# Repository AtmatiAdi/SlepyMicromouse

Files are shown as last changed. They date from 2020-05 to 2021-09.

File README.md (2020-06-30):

# OpisProjektu

Głównym celem projektu jest stworzenie Micromouse który będzie posiadał tylko akcelerometr i żyroskop do rozpoznawania położenia przeszkód i położenia samego robota. Takie rozwiązanie jest niekonwencjonalne gdyż z reguły wszystkie roboty tego typu posiadają czujniki optyczne do wykrywania przeszkód. Micromouse to kategoria robotów których zadaniem jest wydostanie się z labiryntu, ten robot będzie miał takie samo zadanie lecz strategia wyszukiwania wyjścia z labiryntu będzie inna niż standardowo. Robot aby zidentyfikować ściany które są dookoła niego musi w nie stuknąć, nie za mocno by nie uszkodzić labiryntu, a zamantowany akcelerometr wykryje kierunek uderzenia i tak będzie wiadomo gdzie znajduje się przeszkoda. Wykrycie kierunku uderzenia nie jest trywialne więc do tego posłuży specjalnie zamontowana obręcz na sprężynie która da niewielkie możliwości ruchowe, tak aby przy uderzeniu obrącz lekko się przesunęła i akcelerometr na niej zamontowany mógł poprawnie odczytać przesunięcie. Ruchoma obręcz jest potrzebna gdyż zakładamy że koła nie mają poślizgu, więc wykrycie kierunku byłoby utrudnione. żyroskop daje możliwość odczytu obrotu całego robota, wszystko to jest potrzebne ponieważ robot nie będzie miał enkoderów ani innych sensorów które pozwolą sledzić jego przemieszczenie.

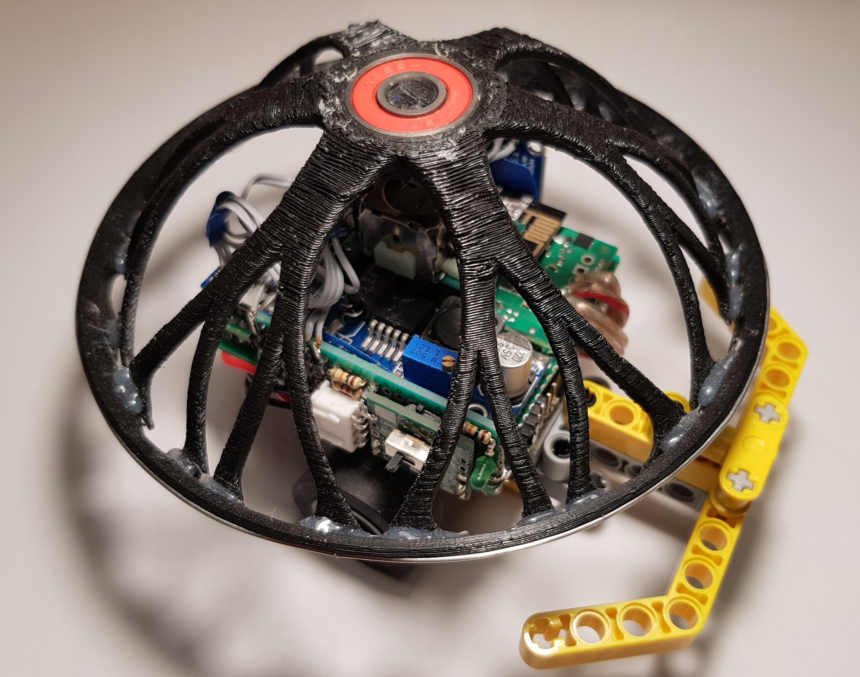
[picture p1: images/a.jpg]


Robot posiada mikrokontroler STM32F103 i sensor MPU-6050. Silniki dobrane będą tak by robot dostatecznie precyzyjnie mógł się poruszać, koła dobrane są tak aby zapewnić przyczepność i móc między innymi w algorytmie wykluczyć poślizg. Dodatkowo wykorzystany zostanie moduł nRF24L01 do komunikacji zdalnej, aby robotem sterować i pobierać od niego informacje sensoryczne, będzie to część na projekt wizualizacja danych sensorycznych. Dodatkowo pomiar napięcia baterii by zabezpieczyć baterie przed rozładowaniem. Moduł mikrokontrolera zawiera stabilizator, tak jak IMU czy moduł radiowy, więc na schemacie zostatał on pominięty.

Sensor MPU-6050 Jest 3 osiowym akcelerometrem i 3 osiowym żyroskopem w jednym, komunikacja z nim przebiega przez magistralę I2C
moduł nRF24L01 To moduł radiowy 2.4Ghz, komunikacja z nim odbywa się poprzez magistralę SPI
Schemat modułowy robota przedstawia rysunek:

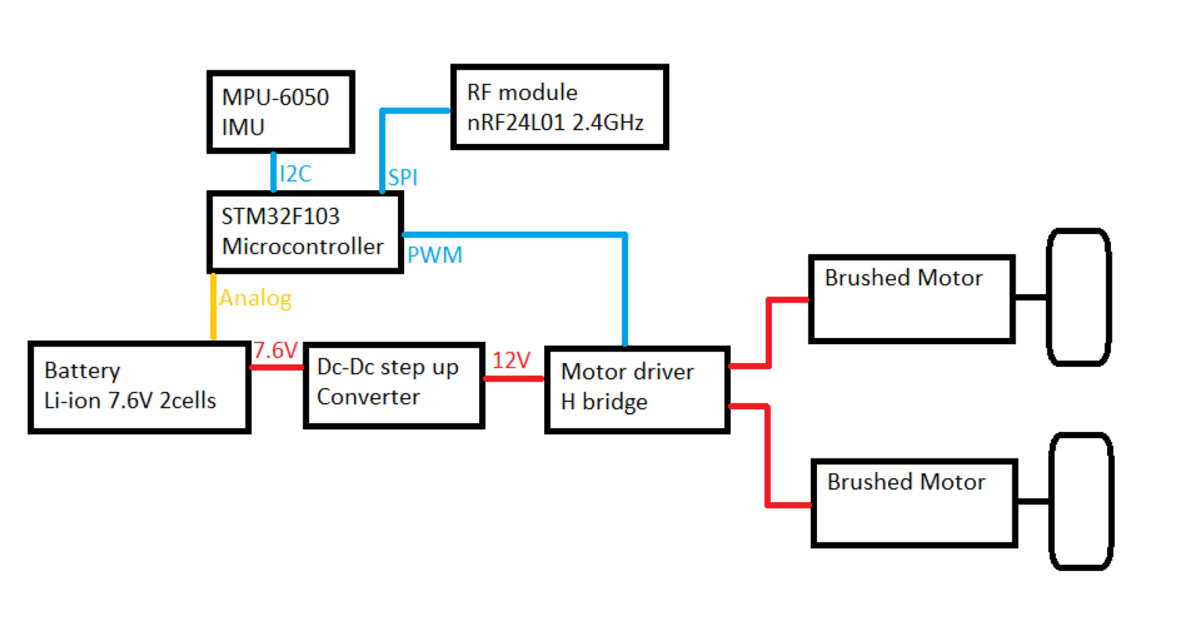
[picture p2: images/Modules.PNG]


# Algorytm Micromouse
Algorytm ma za zadanie wykrywać ściany w labiryncie i zapamiętywać ich ustawienie w pamięci, po odkryciu całego labiryntu wyznaczana będzie ścieżka optymalna z punktu startowego do centrum labiryntu, czyli mety. Następnie robot będzie musiał przebyć wyznaczoną ścieżkę jak najszybciej. Algorytm został zaimplementowany w aplikacji. Takie rozwiązanie bardzo usprawniło tworzenie algorytmu. Istotne jest to że wymiana danych mimo swej prędkości nie jest wstanie zapewnić dokładności w takich operacjach jak przemieszczanie się czy obracanie, liczenie podwójnej całki z tak otrzymywanych danych byłoby bezużyteczne, robot więc posiada funkcje do przemieszczania się i obrotu samodzielnie, zapewnia to dokładność. Jazda o zadane przemieszczenie odbywa się poprzez dostarczenie też informacje o wartości progowej przyspieszenia które oznaczałoby zderzenie się z przeszkodą, niezależnie od przyczyny zakończenia ruchu, robot wysyła wartość przemieszczenia jaką udało mu się wyliczyć na podstawie odczytów z akcelerometru. Podczas obrotu nie podaje się warunku stopu. Uzyskana dokładność obrotu jest bardzo zadowalająca, lecz przemieszczanie się jest obarczone takim błędem że nie możliwe jest zadanie robotowi przemieszczenia większego niż 18 cm (rozmiar jednej komórki labiryntu) bez błędu na tyle dużego który zakłóci działanie algorytmu. Problem ten rozwiązuje sposób przemieszczania się w którym robot zawsze przemieszcza się najdalej jak potrafi, algorytm dostając informację zwrotną dopasowywać ją do labiryntu, jednak takie rozwiązanie powoduje następny problem, robot będzie mógł wpaść w pułapki z których nie będzie dało się w ten sposób wyjechać, rozwiązaniem jest połączenie tych dwóch taktyk tak by algorytm sam decydował o sposobie przemieszczania się.

# Linki

https://youtu.be/gzY4Sm2h51A - Prezentacja ukończenia projektu

https://www.overleaf.com/read/rbngfpkfhwbz - Raport końcowy

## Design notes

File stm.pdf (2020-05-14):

## stm Project Configuration Report

# 1. Description

## 1.1. Project

Project Name | stm
Board Name | No information
Generated with: | STM32CubeMX 4.24.0
Date | 03/13/2020

## 1.2. MCU

MCU Series | STM32F1
MCU Line | STM32F103
MCU name | STM32F103CBTx
MCU Package | LQFP48
MCU Pin number | 48

# 2. Pinout Configuration

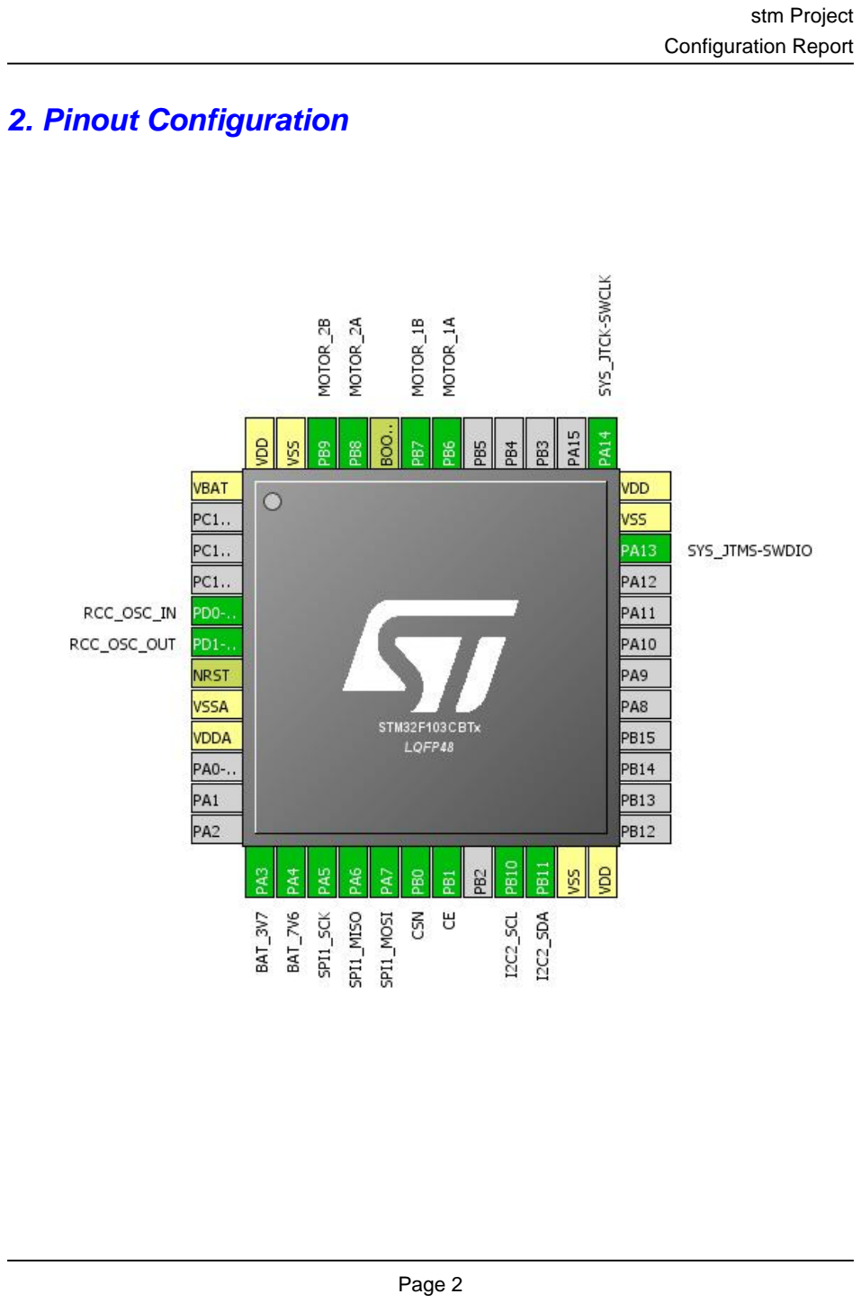
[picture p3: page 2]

# 3. Pins Configuration

Pin Number LQFP48 | Pin Name (function after reset) | Pin Type | Alternate Function(s) | Label
1 | VBAT | Power
5 | PD0-OSC_IN | I/O | RCC_OSC_IN
6 | PD1-OSC_OUT | I/O | RCC_OSC_OUT
7 | NRST | Reset
8 | VSSA | Power
9 | VDDA | Power
13 | PA3 | I/O | ADC1_IN3 | BAT_3V7
14 | PA4 | I/O | ADC1_IN4 | BAT_7V6
15 | PA5 | I/O | SPI1_SCK
16 | PA6 | I/O | SPI1_MISO
17 | PA7 | I/O | SPI1_MOSI
18 | PB0 * | I/O | GPIO_Output | CSN
19 | PB1 * | I/O | GPIO_Output | CE
21 | PB10 | I/O | I2C2_SCL
22 | PB11 | I/O | I2C2_SDA
23 | VSS | Power
24 | VDD | Power
34 | PA13 | I/O | SYS_JTMS-SWDIO
35 | VSS | Power
36 | VDD | Power
37 | PA14 | I/O | SYS_JTCK-SWCLK
42 | PB6 | I/O | TIM4_CH1 | MOTOR_1A
43 | PB7 | I/O | TIM4_CH2 | MOTOR_1B
44 | BOOT0 | Boot
45 | PB8 | I/O | TIM4_CH3 | MOTOR_2A
46 | PB9 | I/O | TIM4_CH4 | MOTOR_2B
47 | VSS | Power
48 | VDD | Power

## * The pin is affected with an I/O function

# 4. Clock Tree Configuration

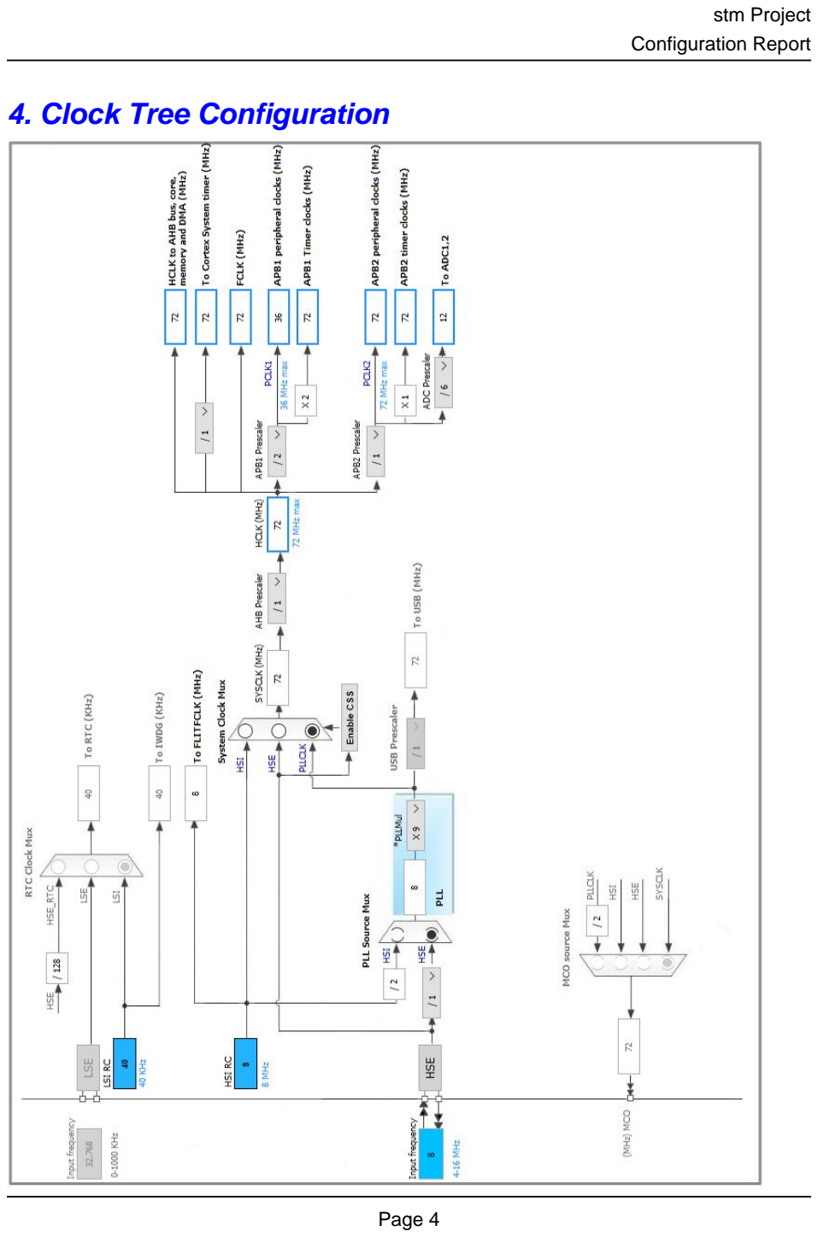
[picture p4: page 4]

# 5. IPs and Middleware Configuration

# 5.1. ADC1

## mode: IN3 mode: IN4

## 5.1.1. Parameter Settings:

### ADCs_Common_Settings:

Mode | Independent mode

### ADC_Settings:

Data Alignment | Right alignment
Scan Conversion Mode | Disabled
Continuous Conversion Mode | Disabled
Discontinuous Conversion Mode | Disabled

### ADC_Regular_ConversionMode:

Enable Regular Conversions | Enable
Number Of Conversion | 1
External Trigger Conversion Source | Regular Conversion launched by software
Rank | 1
Channel | Channel 3
Sampling Time | 1.5 Cycles

### ADC_Injected_ConversionMode:

Number Of Conversions | 0

### WatchDog:

Enable Analog WatchDog Mode | false

# 5.2. I2C2

## I2C: I2C

## 5.2.1. Parameter Settings:

### Master Features:

I2C Speed Mode | Standard Mode
I2C Clock Speed (Hz) | 100000

### Slave Features:

Clock No Stretch Mode | Disabled
Primary Address Length selection | 7-bit
Dual Address Acknowledged | Disabled
Primary slave address | 0
General Call address detection | Disabled

# 5.3. RCC

## High Speed Clock (HSE): Crystal/Ceramic Resonator

## 5.3.1. Parameter Settings:

### System Parameters:

VDD voltage (V) | 3.3
Prefetch Buffer | Enabled
Flash Latency(WS) | 2 WS (3 CPU cycle)

### RCC Parameters:

HSI Calibration Value | 16
HSE Startup Timout Value (ms) | 100
LSE Startup Timout Value (ms) | 5000

# 5.4. SPI1

## Mode: Full-Duplex Master

## 5.4.1. Parameter Settings:

### Basic Parameters:

Frame Format | Motorola
Data Size | 8 Bits
First Bit | MSB First

### Clock Parameters:

Prescaler (for Baud Rate) | 4 *
Baud Rate | 18.0 MBits/s *
Clock Polarity (CPOL) | Low
Clock Phase (CPHA) | 1 Edge

### Advanced Parameters:

CRC Calculation | Disabled

NSS Signal Type | Software

# 5.5. SYS

## Debug: Serial Wire Timebase Source: SysTick

# 5.6. TIM4

## Channel1: PWM Generation CH1 Channel2: PWM Generation CH2 Channel3: PWM Generation CH3 Channel4: PWM Generation CH4

## 5.6.1. Parameter Settings:

### Counter Settings:

Prescaler (PSC - 16 bits value) | 0
Counter Mode | Up
Counter Period (AutoReload Register - 16 bits value ) | 0
Internal Clock Division (CKD) | No Division
auto-reload preload | Disable

### Trigger Output (TRGO) Parameters:

Master/Slave Mode (MSM bit) | Disable (Trigger input effect not delayed)
Trigger Event Selection | Reset (UG bit from TIMx_EGR)

### PWM Generation Channel 1:

Mode | PWM mode 1
Pulse (16 bits value) | 0
Fast Mode | Disable
CH Polarity | High

### PWM Generation Channel 2:

Mode | PWM mode 1
Pulse (16 bits value) | 0
Fast Mode | Disable
CH Polarity | High

### PWM Generation Channel 3:

Mode | PWM mode 1
Pulse (16 bits value) | 0
Fast Mode | Disable
CH Polarity | High

### PWM Generation Channel 4:

Mode | PWM mode 1
Pulse (16 bits value) | 0
Fast Mode | Disable
CH Polarity | High

### * User modified value

# 6. System Configuration

# 6.1. GPIO configuration

IP | Pin | Signal | GPIO mode | GPIO pull/up pull down | Max Speed | User Label
ADC1 | PA3 | ADC1_IN3 | Analog mode | n/a | n/a | BAT_3V7
| PA4 | ADC1_IN4 | Analog mode | n/a | n/a | BAT_7V6
I2C2 | PB10 | I2C2_SCL | Alternate Function Open Drain | n/a | High *
| PB11 | I2C2_SDA | Alternate Function Open Drain | n/a | High *
RCC | PD0-OSC_IN | RCC_OSC_IN | n/a | n/a | n/a
| PD1-OSC_OUT | RCC_OSC_OUT | n/a | n/a | n/a
SPI1 | PA5 | SPI1_SCK | Alternate Function Push Pull | n/a | High *
| PA6 | SPI1_MISO | Input mode | No pull-up and no pull-down | n/a
| PA7 | SPI1_MOSI | Alternate Function Push Pull | n/a | High *
SYS | PA13 | SYS_JTMS-SWDIO | n/a | n/a | n/a
| PA14 | SYS_JTCK-SWCLK | n/a | n/a | n/a
TIM4 | PB6 | TIM4_CH1 | Alternate Function Push Pull | n/a | Low | MOTOR_1A
| PB7 | TIM4_CH2 | Alternate Function Push Pull | n/a | Low | MOTOR_1B
| PB8 | TIM4_CH3 | Alternate Function Push Pull | n/a | Low | MOTOR_2A
| PB9 | TIM4_CH4 | Alternate Function Push Pull | n/a | Low | MOTOR_2B
GPIO | PB0 | GPIO_Output | Output Push Pull | n/a | Low | CSN
| PB1 | GPIO_Output | Output Push Pull | n/a | Low | CE

# 6.2. DMA configuration

## nothing configured in DMA service

# 6.3. NVIC configuration

Interrupt Table | Enable | Preenmption Priority | SubPriority
Non maskable interrupt | true | 0 | 0
Hard fault interrupt | true | 0 | 0
Memory management fault | true | 0 | 0
Prefetch fault, memory access fault | true | 0 | 0
Undefined instruction or illegal state | true | 0 | 0
System service call via SWI instruction | true | 0 | 0
Debug monitor | true | 0 | 0
Pendable request for system service | true | 0 | 0
System tick timer | true | 0 | 0
PVD interrupt through EXTI line 16 | unused
Flash global interrupt | unused
RCC global interrupt | unused
ADC1 and ADC2 global interrupts | unused
TIM4 global interrupt | unused
I2C2 event interrupt | unused
I2C2 error interrupt | unused
SPI1 global interrupt | unused

### * User modified value

# 7. Power Consumption Calculator report

### 7.1. Microcontroller Selection

Series | STM32F1
Line | STM32F103
MCU | STM32F103CBTx
Datasheet | 13587_Rev17

### 7.2. Parameter Selection

Temperature | 25
Vdd | 3.3

# 8. Software Pack Report

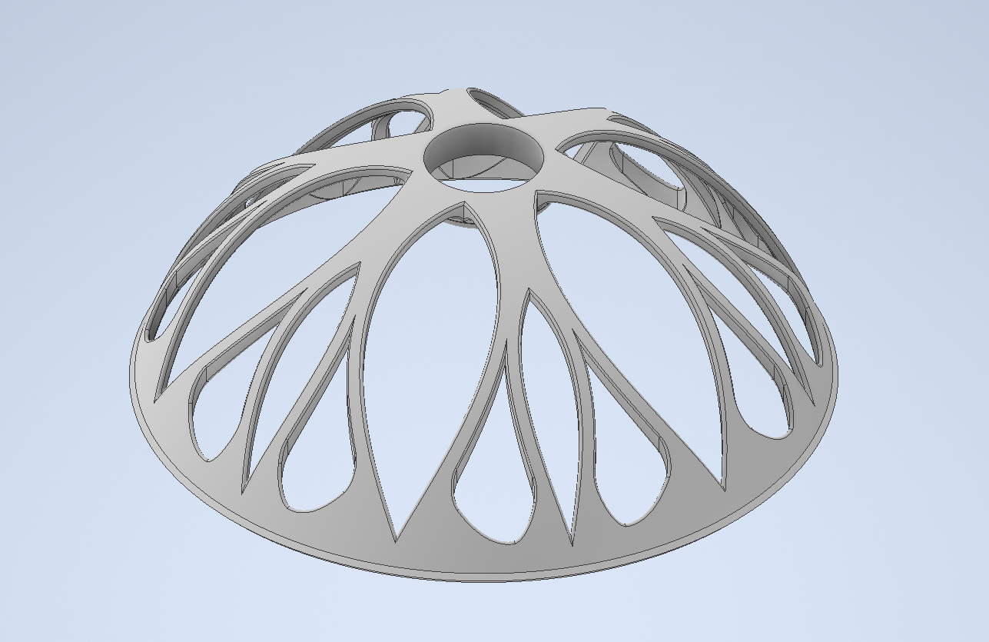
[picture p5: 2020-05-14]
images/obudowa_1.PNG

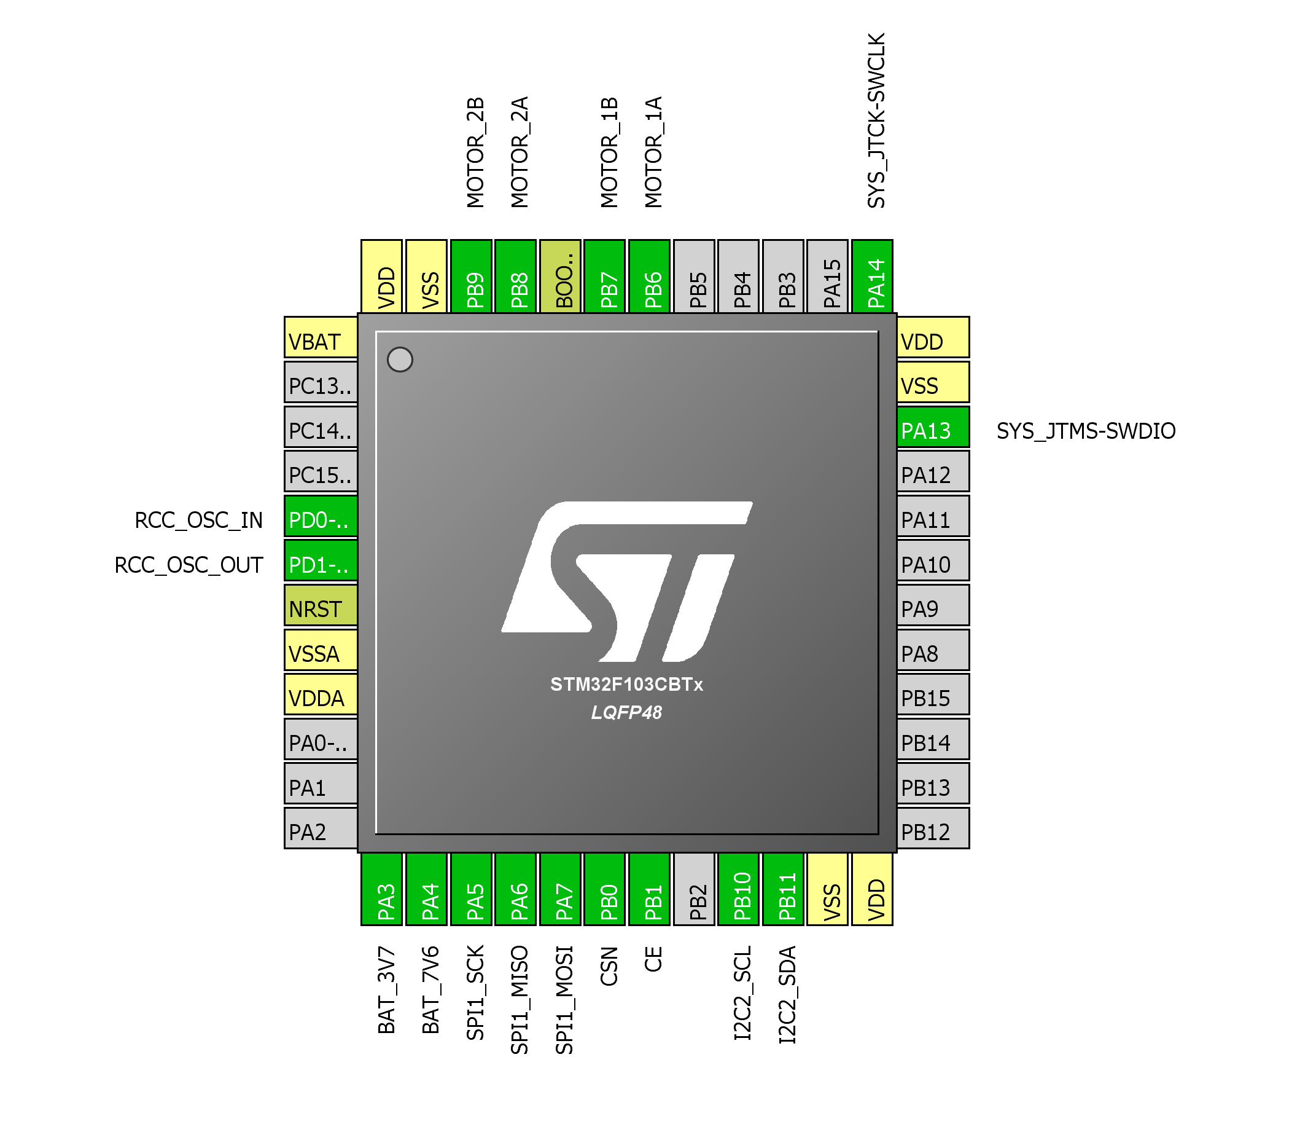
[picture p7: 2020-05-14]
images/cpu.PNG

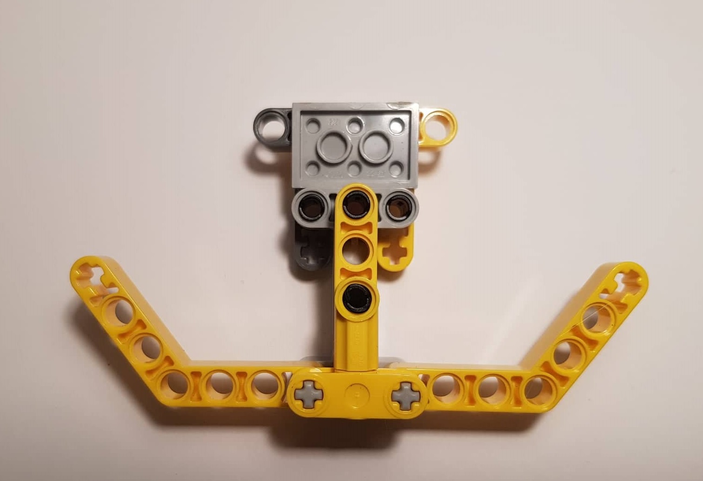
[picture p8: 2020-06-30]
images/lego.jpg

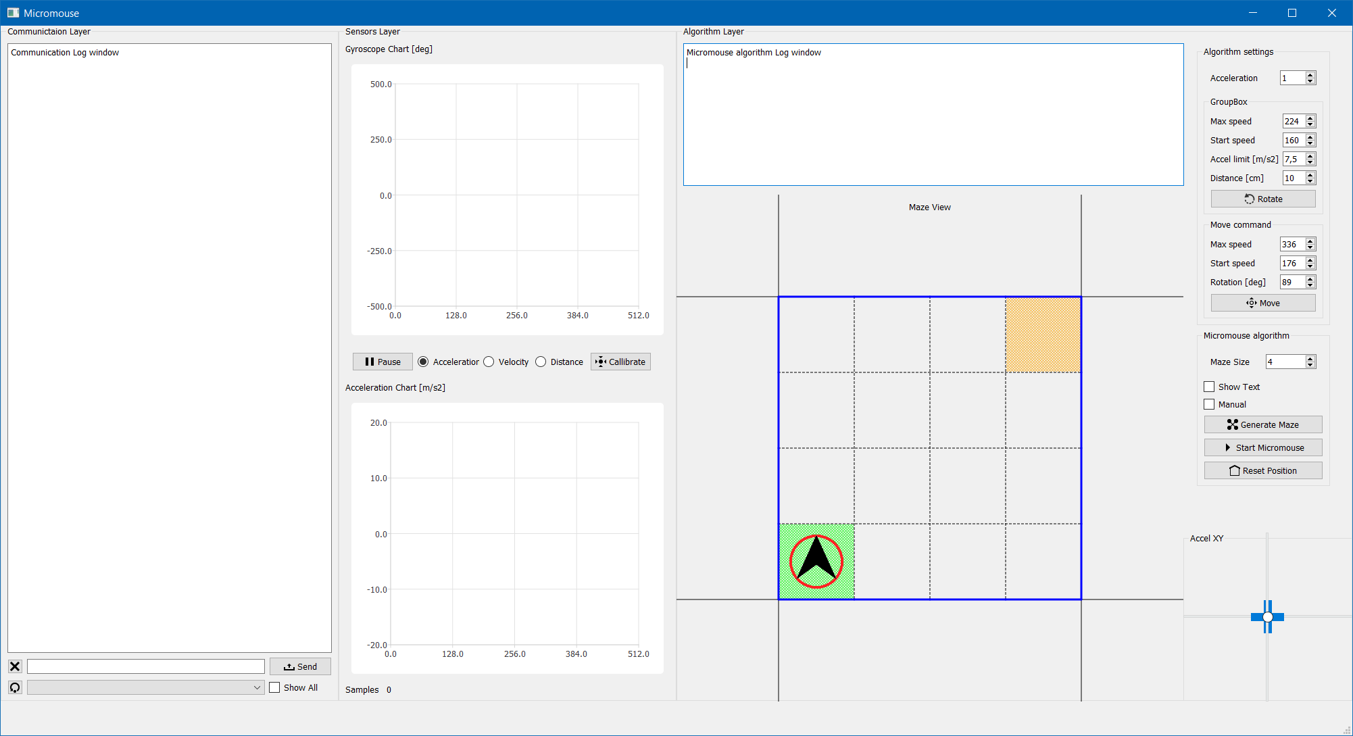
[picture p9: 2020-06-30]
images/apk.PNG

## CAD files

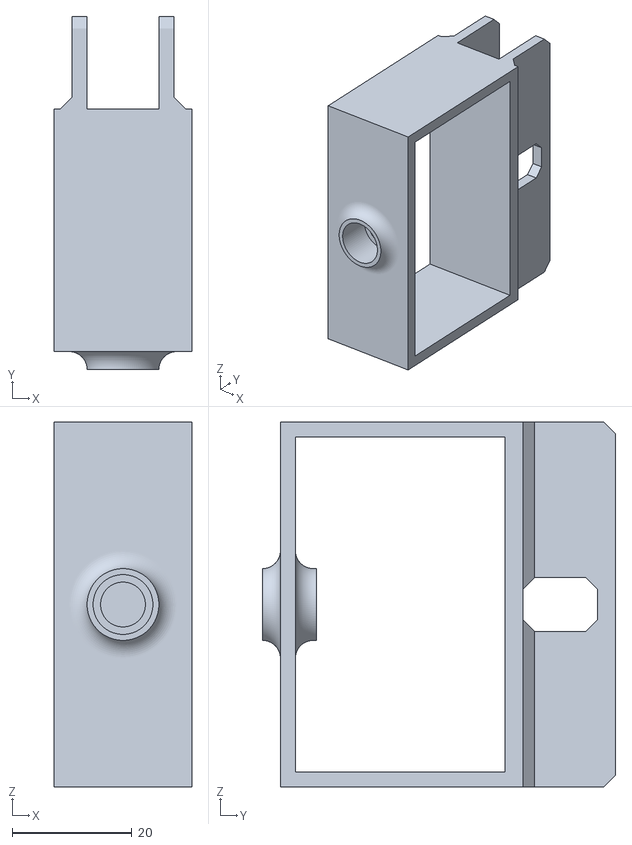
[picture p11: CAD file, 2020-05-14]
Czesci/Koszyk_v2.obj
23.0 x 59.0 x 61.0

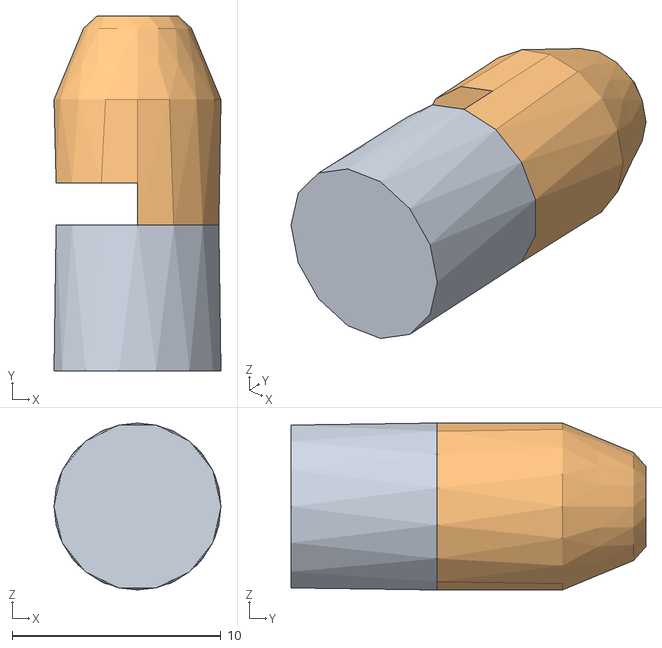
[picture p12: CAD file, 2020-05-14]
Czesci/Czopek.obj
8.00 x 17.0 x 8.00

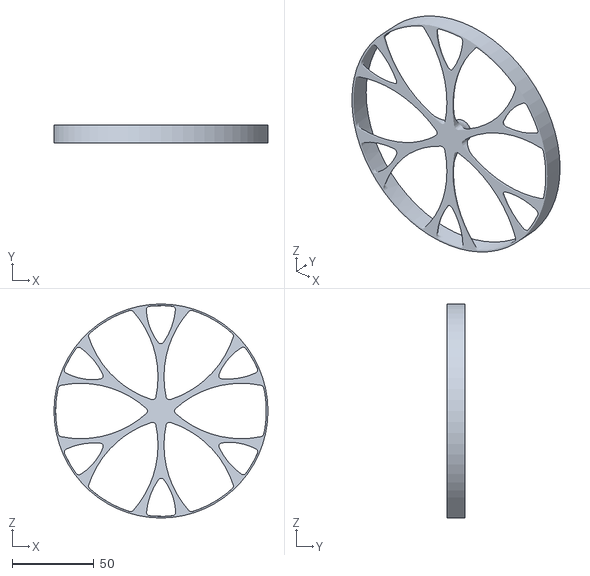
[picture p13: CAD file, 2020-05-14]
Czesci/czujka.obj
131.1 x 11.0 x 131.1

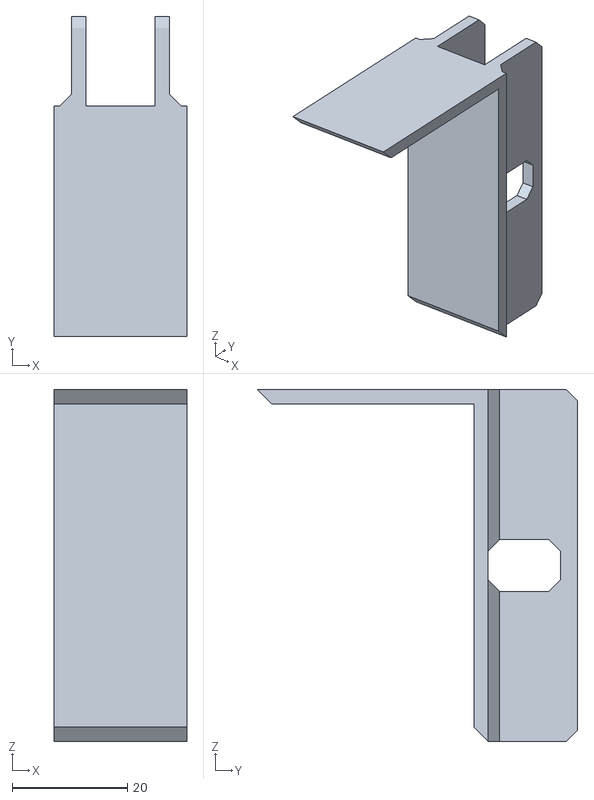
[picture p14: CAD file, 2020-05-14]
Czesci/Koszyk_v2_p1.obj
23.0 x 55.5 x 61.0

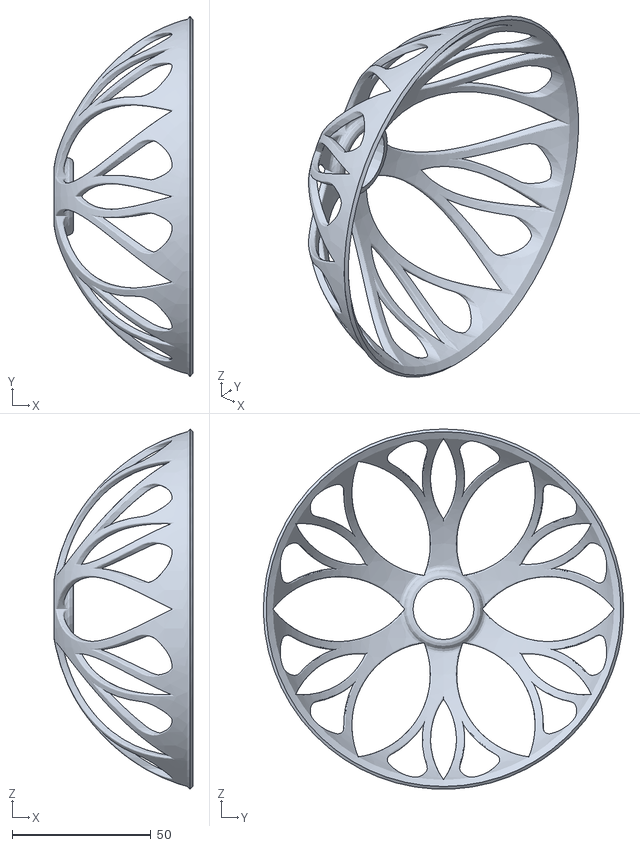
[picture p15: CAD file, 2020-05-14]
Czesci/czujka_v3.obj
50.0 x 130.0 x 129.9

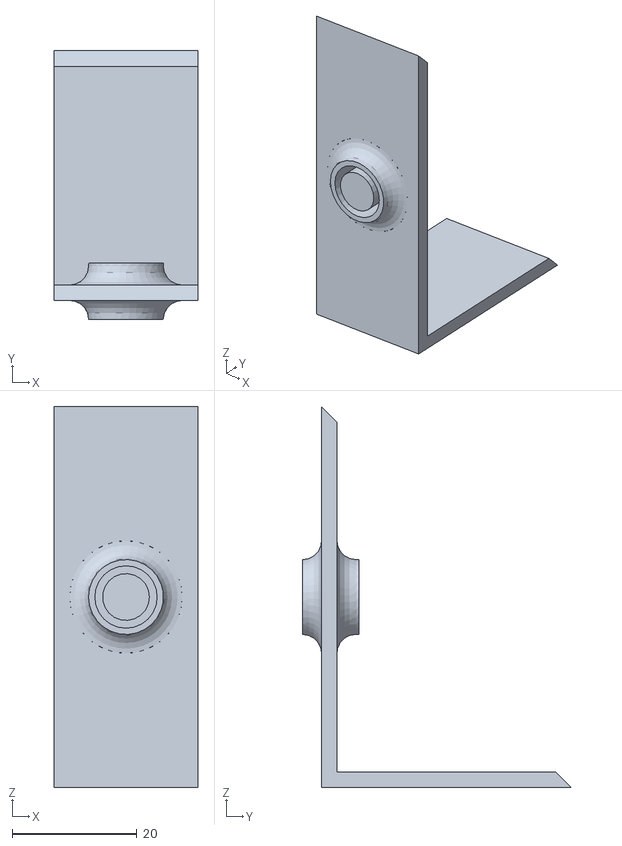
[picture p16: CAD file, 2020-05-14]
Czesci/Koszyk_v2_p2.obj
23.0 x 43.0 x 61.0

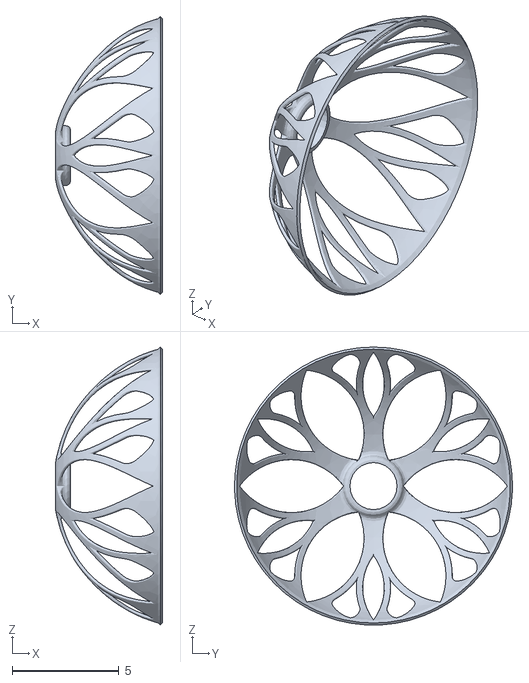
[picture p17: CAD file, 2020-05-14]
Czesci/czujka_v2.stl
5.00 x 13.0 x 13.0

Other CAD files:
Czesci/Koszyk_v2_part.dwg
Czesci/Czopek.ipt
Czesci/Koszyk.ipt
Czesci/Koszyk_v2.ipt
Czesci/Main.ipt
Czesci/OldVersions/Assembly.0011.iam
Czesci/OldVersions/Koszyk.0001.ipt
Czesci/OldVersions/Koszyk_v2.0004.ipt
Czesci/OldVersions/czujka.0005.ipt
Czesci/OldVersions/czujka_v2.0009.ipt
Czesci/OldVersions/mouse.0001.iam
Czesci/czujka.ipt
Czesci/czujka_v2.dwg
Czesci/czujka_v2.ipt
Czesci/czujka_v2.obj
Czesci/frame.ipt
Czesci/mouse.iam

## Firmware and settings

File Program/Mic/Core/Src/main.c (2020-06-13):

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

/* Includes ------------------------------------------------------------------*/
#include "main.h"

/* USER CODE BEGIN Includes */
#include "MY_NRF24.h"
#include "ssd1306.h"
#include "i2c-lcd.h"
#include "string.h"
#include "my_icons.h"
//#include "TJ_MPU6050.h"
#include "AccelGyro.h"

/* USER CODE END Includes */

/* USER CODE BEGIN PTD */
// Funkcja to paczka danych
#define FUNC_ACCEL_GYRO_DATA	128
#define FUNC_JOYSTICK_DATA		129
#define FUNC_ACCEL_GYRO_COMBO	130
// Tryb to trybie pracy
#define MODE_ACCELERATION_BURST 160
#define MODE_VELOCITY_BURST		161
#define MODE_DISTANCE_BURST		162
// Program to jakies zadanie do zrealizowania
#define PROG_CALLIBRATE			192
#define PROG_RESET_VEL_DIST		193
#define PROG_MOVE_BREAK			194
#define PROG_ROTATE				195
// Odpowiedz ze cos gotowe i zwraca wartosc
#define OK						255



/* USER CODE END PTD */

ADC_HandleTypeDef hadc1;

I2C_HandleTypeDef hi2c2;

SPI_HandleTypeDef hspi1;

TIM_HandleTypeDef htim2;
TIM_HandleTypeDef htim3;
TIM_HandleTypeDef htim4;

UART_HandleTypeDef huart1;

void SystemClock_Config(void);
static void MX_GPIO_Init(void);
static void MX_ADC1_Init(void);
static void MX_I2C2_Init(void);
static void MX_SPI1_Init(void);
static void MX_TIM4_Init(void);
static void MX_USART1_UART_Init(void);
static void MX_TIM2_Init(void);
static void MX_TIM3_Init(void);
/* USER CODE BEGIN 0 */
uint64_t PipeAddres = 0x11223344AA;
char Msg[32] = "HI";
char RF_RxData[32];
int Flag = 0;
int Counter = 0;
int mode = MODE_ACCELERATION_BURST;


void MotorSetValue(int16_t Left, int16_t Right)
{
	if (Right > 0) {
		SetPwm(Right, 3);
		SetPwm(0, 4);
	} else {
		SetPwm(0, 3);
		SetPwm(-1 * Right, 4);
	}
	if (Left > 0) {
		SetPwm(Left, 2);
		SetPwm(0, 1);
	} else {
		SetPwm(0, 2);
		SetPwm(-1 * Left, 1);
	}
}

void SetPwm(uint16_t Value, uint16_t Channel) {
    TIM_OC_InitTypeDef sConfigOC;

    sConfigOC.OCMode = TIM_OCMODE_PWM1;
    sConfigOC.Pulse = Value;
    sConfigOC.OCPolarity = TIM_OCPOLARITY_HIGH;
    sConfigOC.OCFastMode = TIM_OCFAST_DISABLE;

    switch(Channel) {
    case 1: {
    	HAL_TIM_PWM_ConfigChannel(&htim4, &sConfigOC, TIM_CHANNEL_1);
		HAL_TIM_PWM_Start(&htim4, TIM_CHANNEL_1);
		break;
    }
    case 2: {
		HAL_TIM_PWM_ConfigChannel(&htim4, &sConfigOC, TIM_CHANNEL_2);
		HAL_TIM_PWM_Start(&htim4, TIM_CHANNEL_2);
		break;
	}
    case 3: {
		HAL_TIM_PWM_ConfigChannel(&htim4, &sConfigOC, TIM_CHANNEL_3);
		HAL_TIM_PWM_Start(&htim4, TIM_CHANNEL_3);
		break;
	}
    case 4: {
		HAL_TIM_PWM_ConfigChannel(&htim4, &sConfigOC, TIM_CHANNEL_4);
		HAL_TIM_PWM_Start(&htim4, TIM_CHANNEL_4);
		break;
	}
    default : {
    	// Blad XDD
    	break;
    }
    }

}

double MapValue(double Val, double FromLow,double FromHigh,double ToLow,double ToHigh){
	return ToLow + ((ToHigh - ToLow) / (FromHigh - FromLow)) * (Val - FromLow);
}

double MapValue2(double input, double input_start,double input_end,double output_start,double output_end) {
	double slope = 1.0 * (output_end - output_start) / (input_end - input_start);
	return output_start + slope * (input - input_start);
}

void HAL_TIM_PeriodElapsedCallback(TIM_HandleTypeDef *htim){
	if (htim->Instance == htim3.Instance){
		Flag = 1;
	}
}

int Serial_Send(uint8_t* Buf, uint32_t *Len){
	CDC_Transmit_FS(Buf, Len);
	return &Len;
}

void SendInt(int Number){
	char in[10], out[10];
	int a = 0;
	int num;
	while ((Number / 10 > 0) || (Number % 10) > 0){
		num = (Number % 10);
		in[a] = num + '0';
		Number = Number / 10;
		a++;
	}
	//for (int b = a - 1; b >= 0; b--) {
	//	out[a - 1 - b] = in[b];
	//}
	if (a > 0) {
		CDC_Transmit_FS(in, a);
	}
}

void SendReturn(short val){
	Msg[0] = OK;
	Msg[1] = val;
	Msg[2] = val >> 8;
	if (NRF24_write(Msg, 3))
	  {
		  //HAL_Delay(1);
		  NRF24_read(RF_RxData, 16);
	  }
}

void AdcRead(int16_t *buf){
	HAL_ADC_Start(&hadc1);
	if (HAL_ADC_PollForConversion(&hadc1, 1000) == HAL_OK) {
		buf[0] = HAL_ADC_GetValue(&hadc1);
	}
	if (HAL_ADC_PollForConversion(&hadc1, 1000) == HAL_OK) {
		buf[1] = HAL_ADC_GetValue(&hadc1);
	}
	if (HAL_ADC_PollForConversion(&hadc1, 1000) == HAL_OK) {
		buf[1] = HAL_ADC_GetValue(&hadc1);
	}
	HAL_ADC_Stop(&hadc1);
}

void UlToStr(char *s, unsigned long bin, unsigned char n)
{
    s += n;
    *s = '\0';

    while (n--)
    {
        *--s = (bin % 10) + '0';
        bin /= 10;
    }
}

void Update_SSD(){
	// Ikona naładowania
	int16_t Val[3];
	AdcRead(Val);
	Val[0] = MapValue(Val[0], 0,4095 , 0, 1000);
	Val[1] = MapValue(Val[1], 0,4095 , 0, 1000);
	//Val[0] -= Val[1];
	char val[5];

	int flat = 0;
	for (int a = 0; a < 2; a++){
		UlToStr(val, Val[a], 5);
		SSD1306_GotoXY (0,a * 20);
		SSD1306_Puts(val, &Font_11x18, 1);
		if (Val[a] > 390) {
			SSD1306_DrawIcon16x16(0+a*20,48, bat3_icon16x16);
		} else if (Val[a] > 360) {
			SSD1306_DrawIcon16x16(0+a*20,48, bat2_icon16x16);
		} else if (Val[a] > 330) {
			SSD1306_DrawIcon16x16(0+a*20,48, bat1_icon16x16);
		} else if (Val[a] > 300) {
			SSD1306_DrawIcon16x16(0+a*20,48, bat0_icon16x16);
		}else {
			SSD1306_DrawIcon16x16(0+a*20,48, cancel_icon16x16);
			flat = 1;
		}
	}
	SSD1306_UpdateScreen();
	SSD1306_Fill(0);
	if (flat) while(1);
}

/* USER CODE END 0 */

/**
  * @brief  The application entry point.
  * @retval int
  */
int main(void)
{
  /* MCU Configuration--------------------------------------------------------*/

  /* Reset of all peripherals, Initializes the Flash interface and the Systick. */
  HAL_Init();

  /* Configure the system clock */
  SystemClock_Config();

  /* Initialize all configured peripherals */
  MX_GPIO_Init();
  MX_ADC1_Init();
  MX_I2C2_Init();
  MX_SPI1_Init();
  MX_TIM4_Init();
  MX_USART1_UART_Init();
  MX_TIM2_Init();
  MX_TIM3_Init();
  /* USER CODE BEGIN 2 */
  // Wyswietlacz
  __HAL_RCC_I2C2_FORCE_RESET();
  __HAL_RCC_I2C2_RELEASE_RESET();
  MX_I2C2_Init();
  __HAL_RCC_I2C2_FORCE_RESET();
  __HAL_RCC_I2C2_RELEASE_RESET();
  MX_I2C2_Init();
  lcd_init();
  SSD1306_Init();
  Update_SSD();

  // Timer
  HAL_TIM_Base_Start_IT(&htim3);

  // NRF
  NRF24_begin(CSN_GPIO_Port, CSN_Pin, CE_Pin, hspi1);
  NRF24_stopListening();
  NRF24_openWritingPipe(PipeAddres);
  NRF24_setAutoAck(true);
  NRF24_setChannel(52);
  NRF24_setPayloadSize(13);
  NRF24_enableDynamicPayloads();
  NRF24_enableAckPayload();

  // MPU

  Init(&hi2c2, &htim2);	// NIC NIE MOZE BYC PO TYM, URUCHAMIA SIE ZEGAR DO CALKOWANIA
  /* USER CODE END 2 */

  /* Infinite loop */
  /* USER CODE BEGIN WHILE */
  while (1)
  {
	  //MotorSetValue(0, 255);
	  Update();
	  switch (mode){
	  case MODE_ACCELERATION_BURST: {
		  GetAcceleration(Msg, 1);
		  break;
	  }
	  case MODE_VELOCITY_BURST: {
		  GetVelocity(Msg, 1);
		  break;
	  }
	  case MODE_DISTANCE_BURST: {
		  GetDistance(Msg, 1);
		  break;
	  }
	  }

	  Msg[0] = FUNC_ACCEL_GYRO_DATA;

	  if (NRF24_write(Msg, 13))
	  {
		  //HAL_Delay(1);
		  NRF24_read(RF_RxData, 16);
	  }
	  //Counter ++;
	  HAL_Delay(1);
	  switch (RF_RxData[0]) {
	  case FUNC_JOYSTICK_DATA: {
		  //HAL_GPIO_TogglePin(LED_GPIO_Port, LED_Pin);
		  int16_t Forward = (unsigned char)RF_RxData[1] | (((uint16_t)RF_RxData[2]) << 8);
		  int16_t Direction = (unsigned char)RF_RxData[3] | (((uint16_t)RF_RxData[4]) << 8);
		  int16_t Left = Forward + Direction;
		  int16_t Right = Forward - Direction;

		  MotorSetValue(Left, Right);
		  break;
	  }
	  case PROG_CALLIBRATE: {
		  Callibrate(RF_RxData[1]);
		  SendReturn(0);
		  break;
	  }
	  case MODE_ACCELERATION_BURST: {
		  mode = MODE_ACCELERATION_BURST;
		  break;
	  }
	  case MODE_VELOCITY_BURST: {
		  mode = MODE_VELOCITY_BURST;
		  break;
	  }
	  case MODE_DISTANCE_BURST: {
		  mode = MODE_DISTANCE_BURST;
		  break;
	  }
	  case PROG_MOVE_BREAK: {
		  // PROG - START - ACCEL - MAX - DIST - STOP
		  short SSpeed = (unsigned char)RF_RxData[1] | (((uint16_t)RF_RxData[2]) << 8);
		  short ASpeed = (unsigned char)RF_RxData[3] | (((uint16_t)RF_RxData[4]) << 8);
		  short MSpeed = (unsigned char)RF_RxData[5] | (((uint16_t)RF_RxData[6]) << 8);
		  short Dist = (unsigned char)RF_RxData[7] | (((uint16_t)RF_RxData[8]) << 8);
		  short ReturnDist = 0;
		  short Stop = (unsigned char)RF_RxData[9] | (((uint16_t)RF_RxData[10]) << 8);
		  double Rot;
		  double P = 0.02, I = 0.1;
		  Callibrate(255);
		  Update();
		  /*
		  if (Dist > 0){
			  while(ReturnDist < Dist){
				  Rot = P * Acceleration[5] + I * Velocity[5]/1000000.0;
				  if (SSpeed < MSpeed) {
					  MSpeed -= ASpeed;
				  }
				  MotorSetValue(-MSpeed -Rot, -MSpeed + Rot);
				  ReturnDist = Distance[0]/1000000000000;
				  Update();
				  if ((Acceleration[0] > Stop) || (Acceleration[1] > Stop) || (Acceleration[2] > Stop)){
					  break;	// Uderzenie
				  }
			  }
		  } else {
			  while(ReturnDist > Dist){
				  Rot = P * Acceleration[5] + I * Velocity[5]/1000000.0;
				  if (SSpeed < MSpeed) {
					  MSpeed -= ASpeed;
				  }
				  MotorSetValue(MSpeed -Rot, MSpeed + Rot);
				  ReturnDist = Distance[0]/1000000000000;
				  Update();
				  if ((Acceleration[0] > Stop) || (Acceleration[1] > Stop) || (Acceleration[2] > Stop)){
					  break;	// Uderzenie
				  }
			  }
		  }
		  MotorSetValue(0, 0);
		  SendReturn(ReturnDist);
		  break;
	  }*/
	  if (Dist > 0){
			  while(ReturnDist < Dist){
				  Rot = P * Acceleration[5] + I * Velocity[5]/1000000.0;
				  if (SSpeed < MSpeed) {
					  SSpeed += ASpeed;
				  }
				  MotorSetValue(-SSpeed -Rot, -SSpeed + Rot);
				  ReturnDist = Distance[0]/1000000000000;
				  Update();
				  if ((Acceleration[0] > Stop) || (Acceleration[1] > Stop) || (Acceleration[2] > Stop)){
					  break;	// Uderzenie
				  }
			  }
		  } else {
			  while(ReturnDist > Dist){
				  Rot = P * Acceleration[5] + I * Velocity[5]/1000000.0;
				  if (SSpeed < MSpeed) {
					  SSpeed += ASpeed;
				  }
				  MotorSetValue(SSpeed -Rot, SSpeed + Rot);
				  ReturnDist = Distance[0]/1000000000000;
				  Update();
				  if ((Acceleration[0] > Stop) || (Acceleration[1] > Stop) || (Acceleration[2] > Stop)){
					  break;	// Uderzenie
				  }
			  }
		  }
		  MotorSetValue(0, 0);
		  SendReturn(ReturnDist);
		  break;
	  }
	  case PROG_ROTATE: {
		  // PROG - START - ACCEL - MAX - ANGLE
		  short SSpeed = (unsigned char)RF_RxData[1] | (((uint16_t)RF_RxData[2]) << 8);
		  short ASpeed = (unsigned char)RF_RxData[3] | (((uint16_t)RF_RxData[4]) << 8);
		  short MSpeed = (unsigned char)RF_RxData[5] | (((uint16_t)RF_RxData[6]) << 8);
		  short Angle = (unsigned char)RF_RxData[7] | (((uint16_t)RF_RxData[8]) << 8);
		  short ReturnAngle = 0;
		  Callibrate(255);
		  Update();
		  if (Angle > 0){
			  while(ReturnAngle < Angle){
				  if (SSpeed <= MSpeed) {
					  MotorSetValue(MSpeed, -MSpeed);
					  MSpeed -= ASpeed;
				  }
				  ReturnAngle = Velocity[5]/1000000;
				  Update();
			  }
		  } else {
			  while(ReturnAngle > Angle){
				  if (SSpeed <= MSpeed) {
					  MotorSetValue(-MSpeed, MSpeed);
					  MSpeed -= ASpeed;
				  }
				  ReturnAngle = Velocity[5]/1000000;
				  Update();
			  }
		  }
		  MotorSetValue(0, 0);
		  SendReturn(ReturnAngle);
		  break;
	  }
	  }

	  if (Flag == 1) {
		  HAL_GPIO_TogglePin(LED_GPIO_Port, LED_Pin);
		  //char c[3] = {'<', '-'};
		  //SendInt(Counter);
		  //Serial_Send(c, 2);
		  //Counter = 0;
		  Flag = 0;
	  }
	  //HAL_Delay(1);
    /* USER CODE END WHILE */

    /* USER CODE BEGIN 3 */
  }
  /* USER CODE END 3 */
}

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


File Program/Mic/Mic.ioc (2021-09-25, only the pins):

Mcu.UserName=STM32F103CBTx
PA10.Signal=USART1_RX
PA13.Signal=SYS_JTMS-SWDIO
PA14.Signal=SYS_JTCK-SWCLK
PA2.GPIO_Label=VBUS_3V3
PA2.Signal=ADCx_IN2
PA3.GPIO_Label=BAT_3V7
PA3.Signal=ADCx_IN3
PA4.GPIO_Label=BAT_7V6
PA4.Signal=ADCx_IN4
PA5.Signal=SPI1_SCK
PA6.Signal=SPI1_MISO
PA7.Signal=SPI1_MOSI
PA9.Signal=USART1_TX
PB0.GPIO_Label=CSN
PB0.Signal=GPIO_Output
PB1.GPIO_Label=CE
PB1.Signal=GPIO_Output
PB10.Signal=I2C2_SCL
PB11.Signal=I2C2_SDA
PB6.GPIO_Label=MOTOR_1A
PB6.Signal=S_TIM4_CH1
PB7.GPIO_Label=MOTOR_1B
PB7.Signal=S_TIM4_CH2
PB8.GPIO_Label=MOTOR_2A
PB8.Signal=S_TIM4_CH3
PB9.GPIO_Label=MOTOR_2B
PB9.Signal=S_TIM4_CH4
PC13-TAMPER-RTC.GPIO_Label=LED
PC13-TAMPER-RTC.Signal=GPIO_Output
PD0-OSC_IN.Signal=RCC_OSC_IN
PD1-OSC_OUT.Signal=RCC_OSC_OUT

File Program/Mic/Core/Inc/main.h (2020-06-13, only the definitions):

#define MOTOR_PRESCALLER 72-1
#define MOTOR_COUNTER 1024-1
#define TIM_PRE 72000-1
#define LED_Pin GPIO_PIN_13
#define LED_GPIO_Port GPIOC
#define VBUS_3V3_Pin GPIO_PIN_2
#define VBUS_3V3_GPIO_Port GPIOA
#define BAT_3V7_Pin GPIO_PIN_3
#define BAT_3V7_GPIO_Port GPIOA
#define BAT_7V6_Pin GPIO_PIN_4
#define BAT_7V6_GPIO_Port GPIOA
#define CSN_Pin GPIO_PIN_0
#define CSN_GPIO_Port GPIOB
#define CE_Pin GPIO_PIN_1
#define CE_GPIO_Port GPIOB
#define MOTOR_1A_Pin GPIO_PIN_6
#define MOTOR_1A_GPIO_Port GPIOB
#define MOTOR_1B_Pin GPIO_PIN_7
#define MOTOR_1B_GPIO_Port GPIOB
#define MOTOR_2A_Pin GPIO_PIN_8
#define MOTOR_2A_GPIO_Port GPIOB
#define MOTOR_2B_Pin GPIO_PIN_9
#define MOTOR_2B_GPIO_Port GPIOB

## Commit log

2020-05-14 Wprowadzono projekt
    [Assembly.0011.iam, Czopek.ipt, Czopek.obj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]
2020-05-19 Update
    Przeniesiono ruch i obrót do robota, regulator PI

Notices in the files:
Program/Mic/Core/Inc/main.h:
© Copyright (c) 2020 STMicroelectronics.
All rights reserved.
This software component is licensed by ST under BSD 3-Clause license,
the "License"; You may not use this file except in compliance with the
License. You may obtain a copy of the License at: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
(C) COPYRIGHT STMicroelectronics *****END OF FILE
